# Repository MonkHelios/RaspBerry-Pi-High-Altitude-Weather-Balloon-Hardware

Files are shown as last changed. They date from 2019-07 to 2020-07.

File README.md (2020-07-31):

# Raspberry Pi Powered High Altitude Weather Balloon:

**The hardware of the weather balloon or the payload section is structured as a six layered stack of Raspberry Pi hats.**

---



- [x] The first layer is a _**Raspberry Pi**_ which manages operation of all other stacks and undertakes necessary processing tasks.
- [x] To power the entire stack we have a high current DC-DC converter as a _**power delivery unit**_ which accepts 1S LiPo or LiIon batteries as input and outputs a steady 5V and allows a maximum current draw of 7A.
- [x] For telemetry and other communication purposes we are using a _**CC1125 based RF board**_.
- [x] The next stack comprises of a _**GSM board**_ for non LOS communication at lower altitudes and a _**GPS board**_ for tracking the balloon and for easy retrieval. Since both of these are using the same serial channel of the Raspberry Pi, multiplexing and demultiplexing were necessary. This was facilitated by a _**Mux Demux board**_ which had the ability to select one peripheral among the two.
- [ ] Finally on top of the GPS hat we have the _**sensor hat**_.

---

## 1. Power Delivery Board (PiPo):

To run the essential hardware stacks a power delivery system more capable than a Raspberry Pi's internal power distribution was required. A design of a power distribution stack which could supply a high enough current with stability was adopted. The board was powered with a 3.7V LiIon or LiPo cell, its output was a constant 5V with a maximum allowed current of 7A. Our required peak current was 5A so, a 2A headroom was kept. The design was built around the _**LTC1871-1**_ - a wide input range, current mode, boost, flyback or SEPIC controller that drives an N-channel power MOSFET and requires very few external components.

### 1.1. Schematic:

<p align="center">
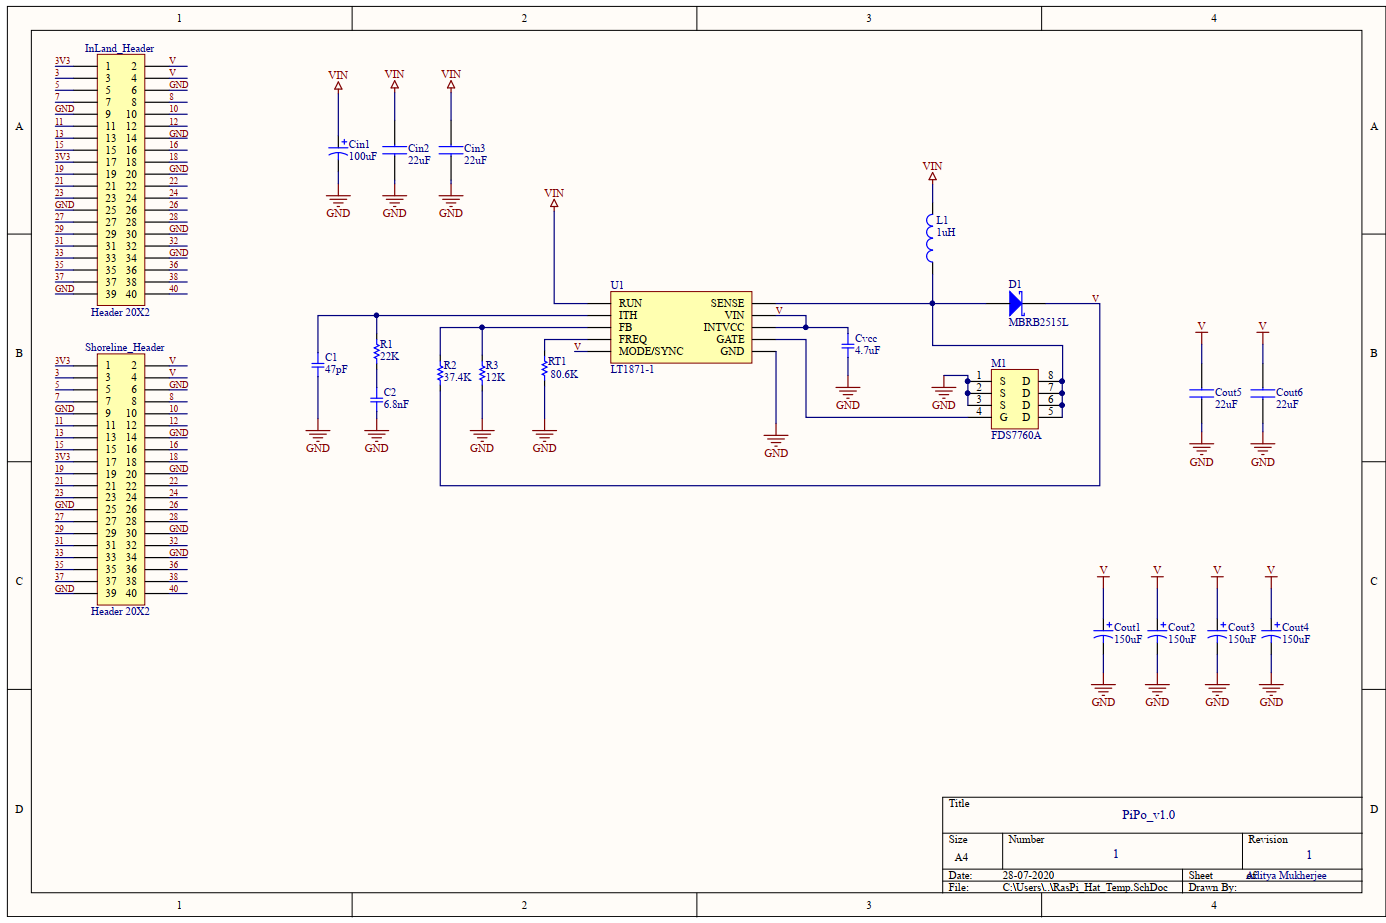
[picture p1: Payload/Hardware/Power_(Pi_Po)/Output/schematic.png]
  
</p>

[Link to PDF](https://github.com/MonkHelios/RaspBerry-Pi-High-Altitude-Weather-Balloon-Hardware/blob/master/Payload/Hardware/Power_(Pi_Po)/Output/schematic.pdf)

### 1.2. Composite:

<p align="center">
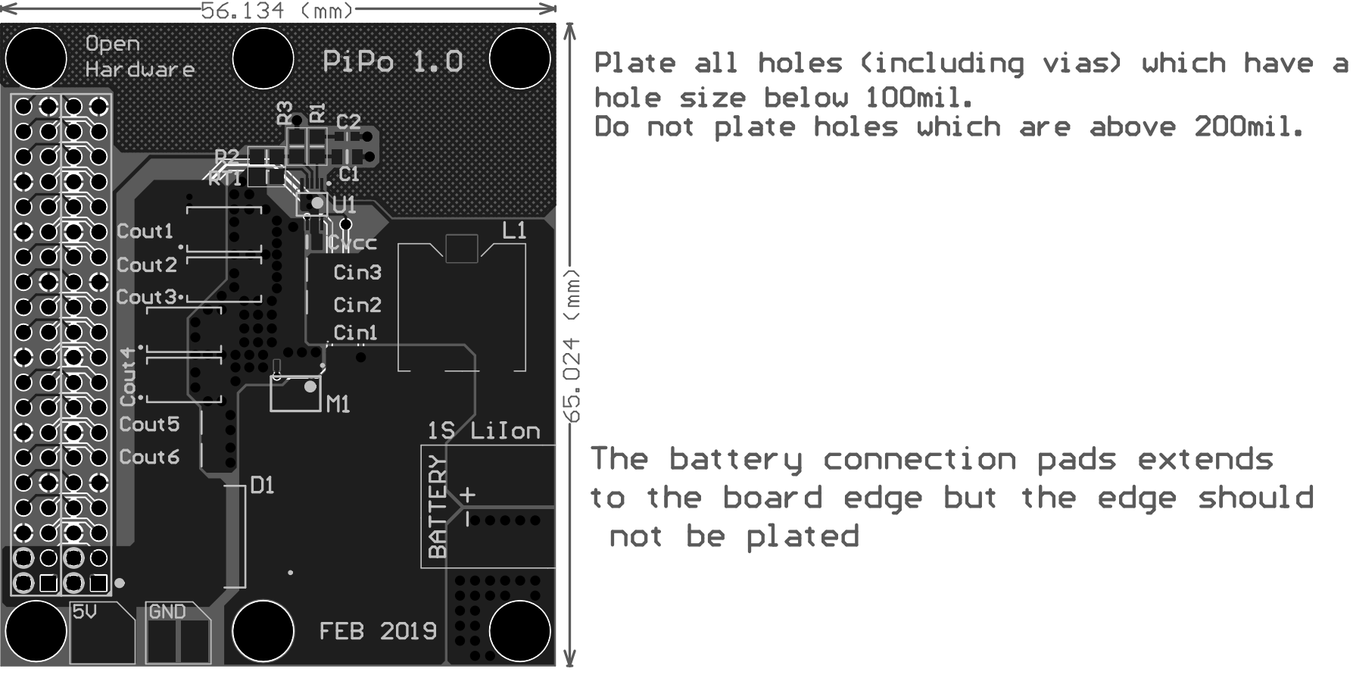
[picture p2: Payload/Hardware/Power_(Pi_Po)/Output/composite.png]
  
</p>

### 1.3. Assembly:

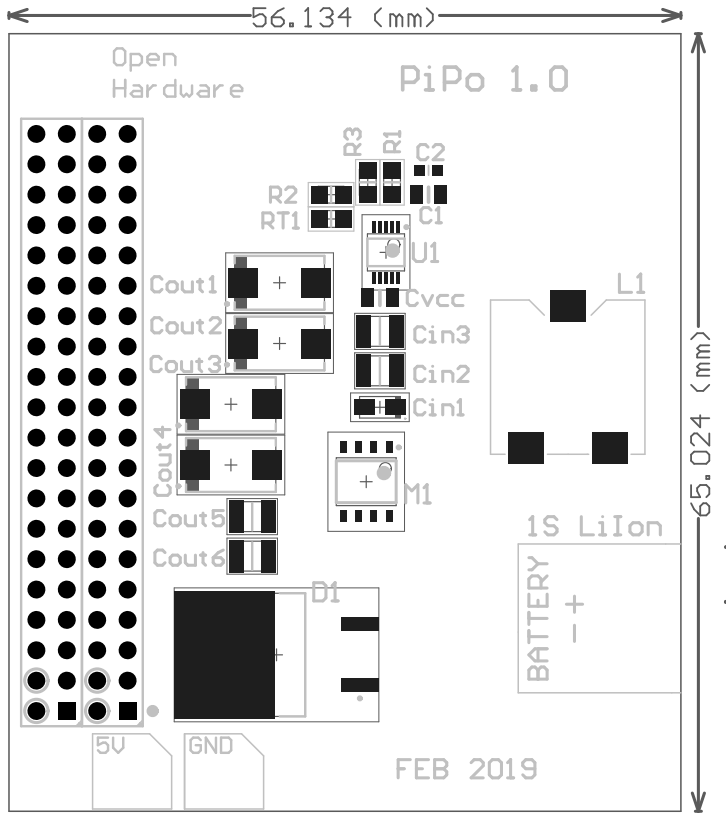
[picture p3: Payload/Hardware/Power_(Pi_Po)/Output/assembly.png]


**Comments on Revision 1.0 -** Assistance regarding _PCB layout, component placing & the schematic design_ was taken from the corresponding datasheets. Output voltage was as expected, as well as the ability to supply high currents. However, on probing the output with and oscilloscope it was found that the output waveform was quite noisy and had significant switching noise at the frequency of the used DC-DC converter. 

<br>

It was concluded that PCB layout and component placement were the culprits for induction of switching noise _(To be addressed in rev 2.0)_. Hence, I would not recommend following the component placement and PCB layout guides present in _**LTC1871-1's**_ datasheet. Instead, Understand the guidelines given and apply common mutual induction principles while designing the output section. 

<br>

<br>

---

## 2. Transceiver Board (LinkBerry):

For telemetry, real time location update and live image/video feed a point to point long distance RF link was designed and fabricated which is based on _Texas Instrument's_ _**CC1125**_ - a single chip, fully integrated narrow band RF transceiver. Coupled with a front end module (FEM) - _Qorvo's **RFFM6403**_, the board has a maximum output power level of **30dBm**. The FEM has inbuilt selectable power amplifier (PA) for transmission and a low noise amplifier (LNA) for reception. This communication stack acts as a bridge between the Pi's SPI bus and the unguided RF encoded & modulated data. In other words this encodes, modulates & transmits data received over the SPI bus (from the Pi). Also it decodes data received over its RF link and sends it through the SPI bus.
This is a 4 layer board since this includes mixed signal components, hence, strict PCB layout requirements. Also a thinner dielectric (prepreg) between the 50 Ohm RF traces and the GND plane allows for narrower RF microstrip lines for a given impedance. So, the layer stackup is important to keep in mind while designing.

### 2.1. Schematic:

[Link to PDF](https://github.com/MonkHelios/RaspBerry-Pi-High-Altitude-Weather-Balloon-Hardware/blob/master/Payload/Hardware/Transceiver_(LinkBerry)/Output/Radio.pdf)
_because component labels are too small for an image here._

`CC1125's datasheet followed for 50 Ohm matching`

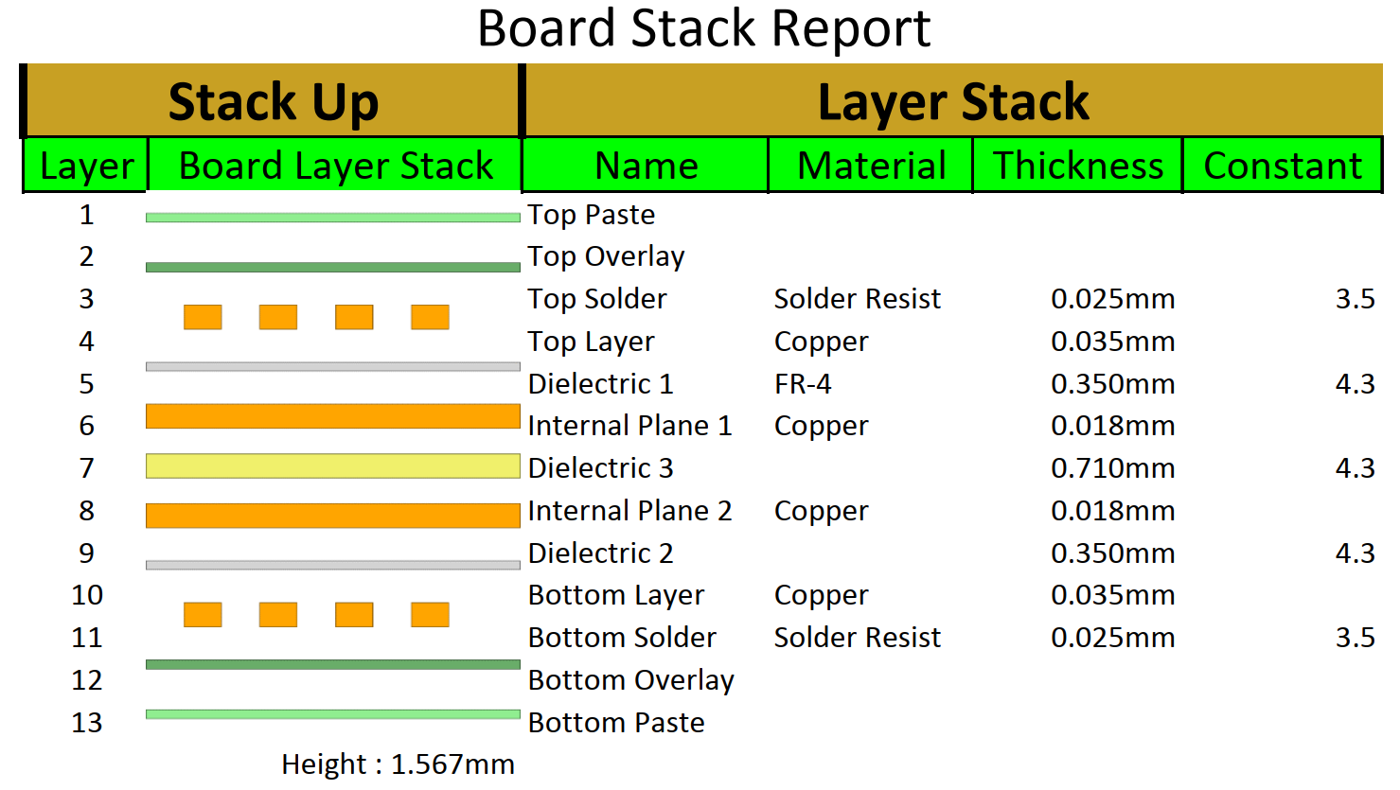
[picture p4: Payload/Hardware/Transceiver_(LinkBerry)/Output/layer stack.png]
### 2.2. Layer Stackup: 

- Top layer - separated digital and analog signals, most important signals are routed on this layer.
- Internal plane 1 - GND plane.
- Internal plane 2 - Power plane includes 3.3V, 3.6V & 5V polygons.
- Bottom layer - less important digital signals, traces which did not fit on the top layer, bridges and a GND polygon.

<br>

### 2.3. PCB layers:

<br>

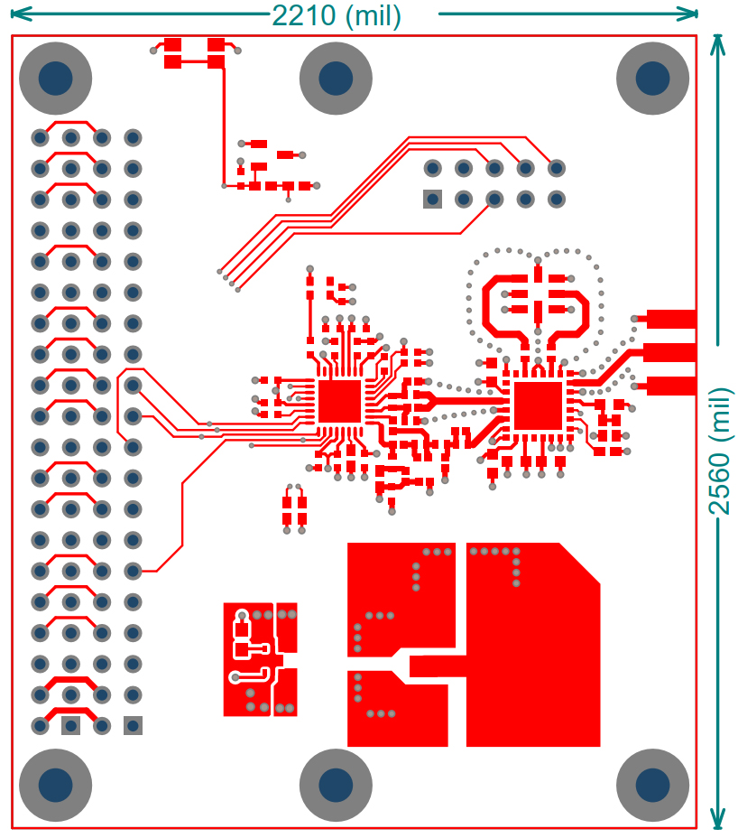
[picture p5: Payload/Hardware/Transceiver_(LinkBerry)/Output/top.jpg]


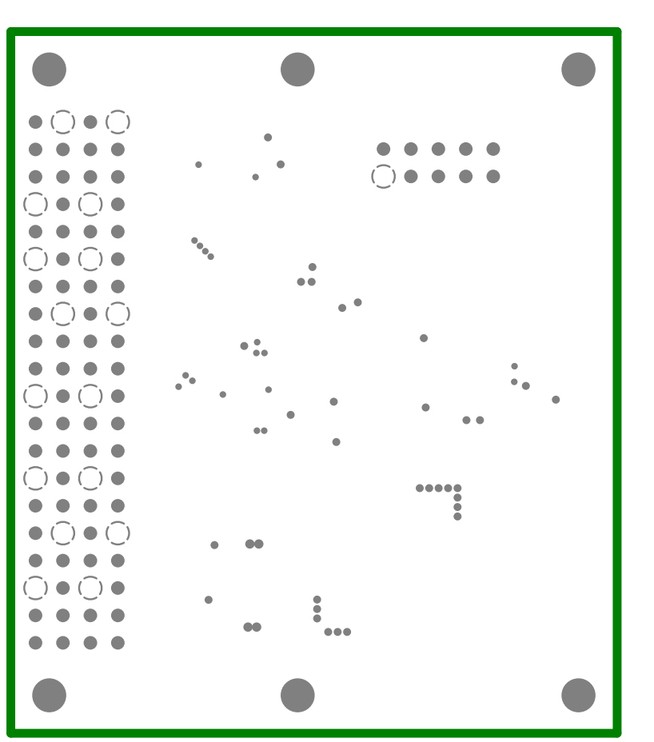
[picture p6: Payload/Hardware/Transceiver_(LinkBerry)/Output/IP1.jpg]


<p align="center">
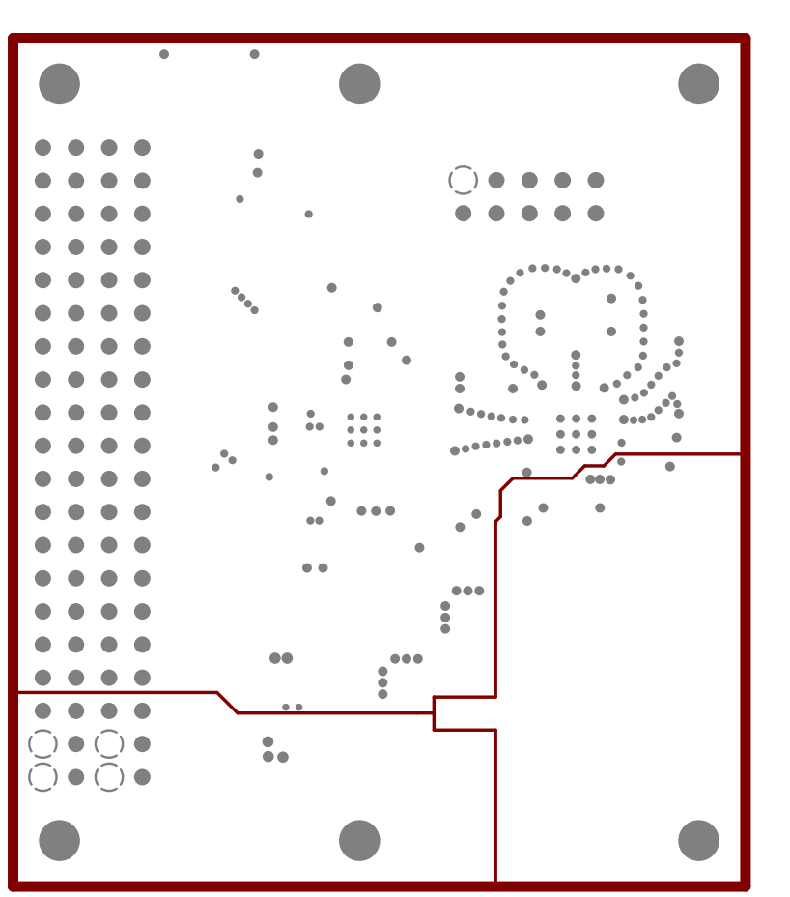
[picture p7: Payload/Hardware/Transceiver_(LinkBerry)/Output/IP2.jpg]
  
</p>

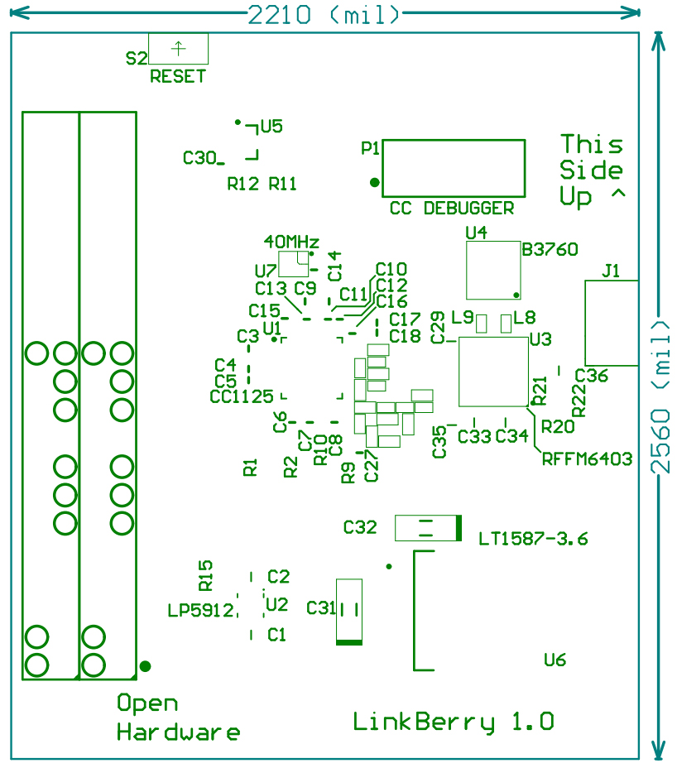
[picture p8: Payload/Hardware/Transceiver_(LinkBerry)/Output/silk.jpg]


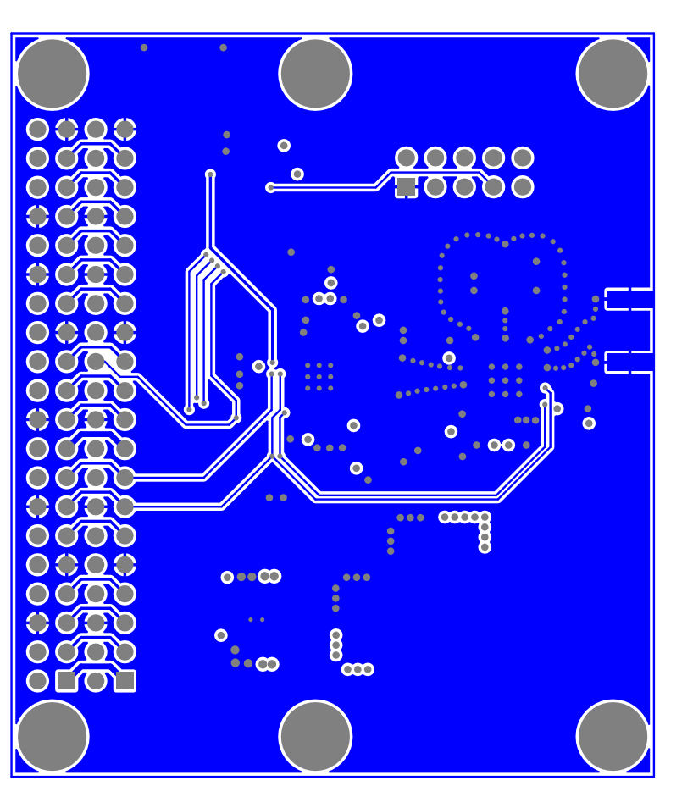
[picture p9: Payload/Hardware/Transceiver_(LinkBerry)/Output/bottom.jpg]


<p align="center">
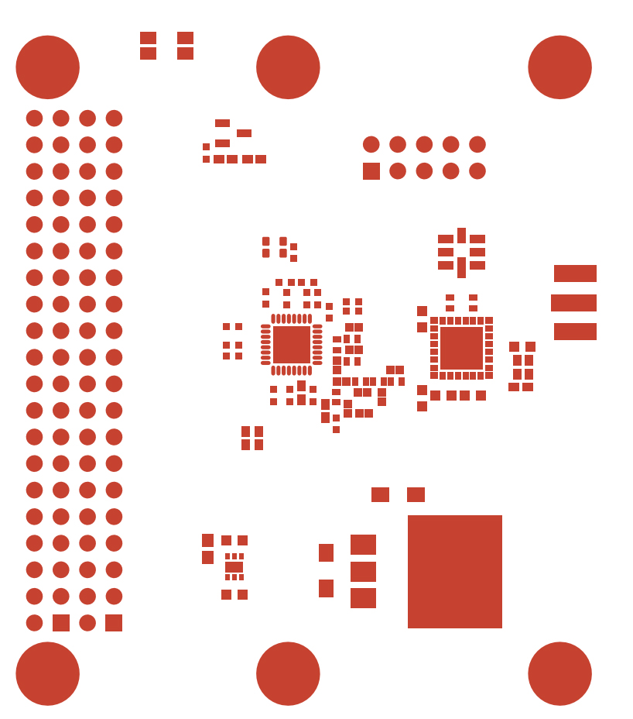
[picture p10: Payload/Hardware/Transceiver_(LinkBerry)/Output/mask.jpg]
  
</p>

<br>

<br>

### 2.4. Images:

<br>





<p align="center">
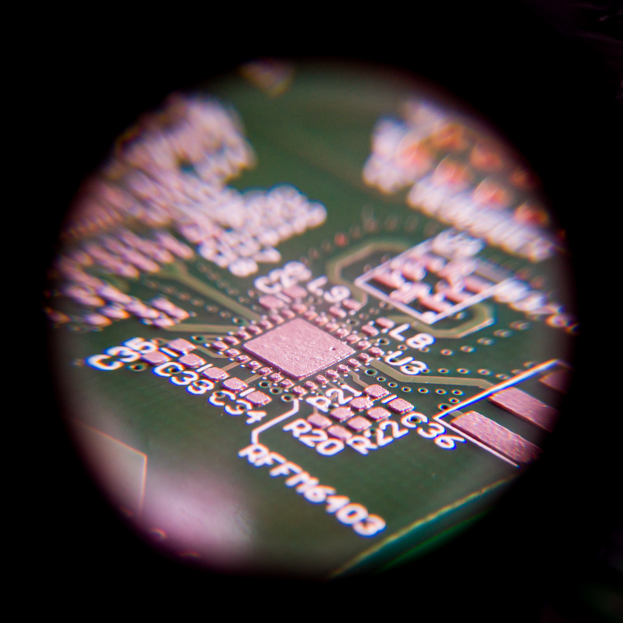
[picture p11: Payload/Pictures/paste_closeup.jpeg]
  
</p>
<br>

<br>

<br>

---

## 3. Multiplexer Board (PiMux):

This is a rather minimal 2:1 MUX board built around _**ISL54220**_ - a single supply dual 2:1 multiplexer that can operate from a single 2.7V to 5.5V supply. This multiplexes the two serial peripherals - GSM & GPS boards and enables them to be used one at a time on the single serial bus available on the Raspberry Pi. Data rates aren't a bottle neck as this IC was designed for USB purposes (480 Mbps).

### 3.1. Functional Diagram:

<p align="center">
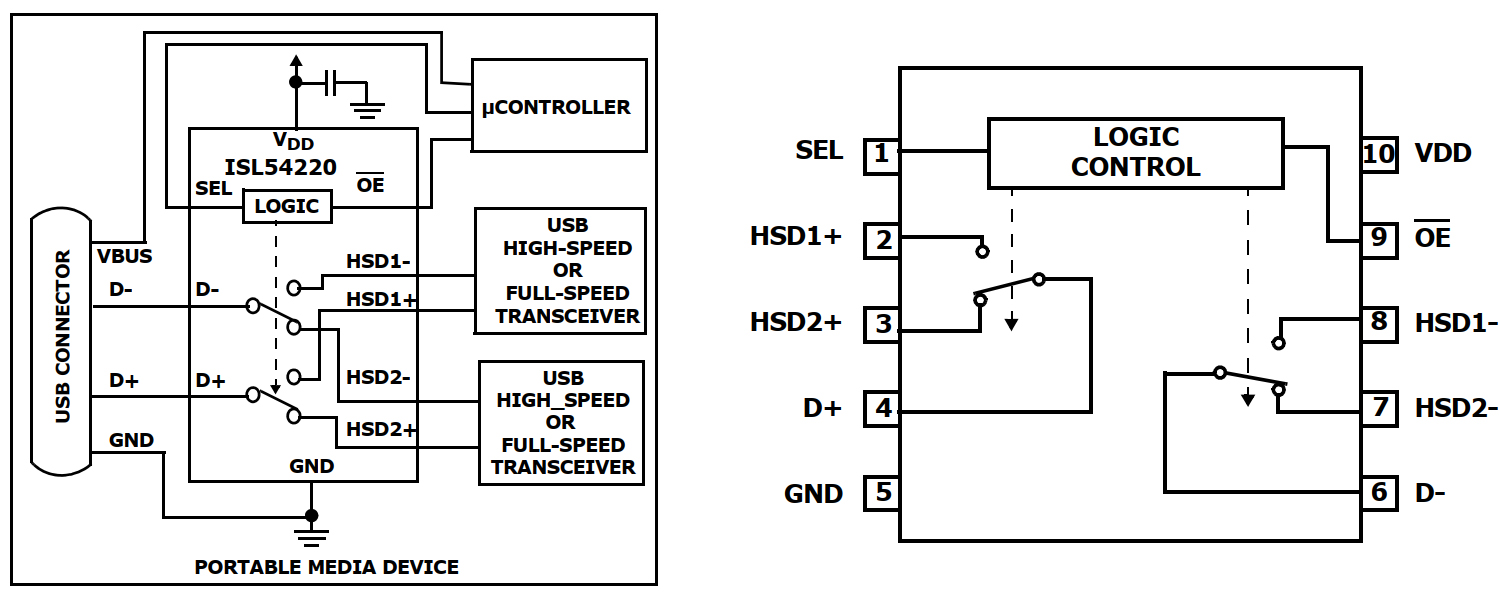
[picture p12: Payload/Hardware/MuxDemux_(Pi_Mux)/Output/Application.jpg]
  
</p>

<br>

### 3.2. Truth Table: 

<p align="center">
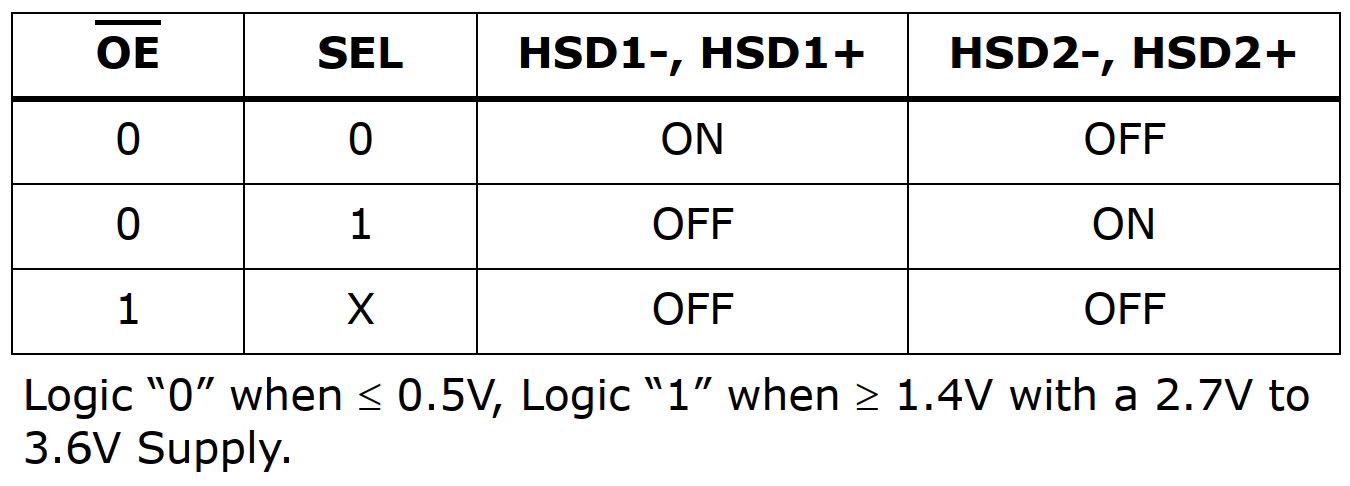
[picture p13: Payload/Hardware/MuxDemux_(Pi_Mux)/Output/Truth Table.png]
  
</p>

<br>

### 3.3. Schematic:

<p align="center">
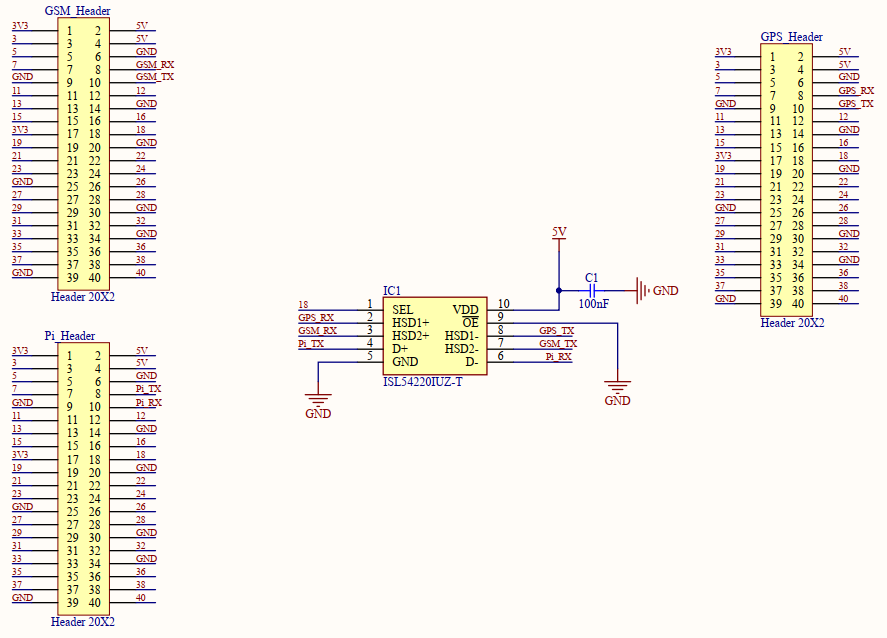
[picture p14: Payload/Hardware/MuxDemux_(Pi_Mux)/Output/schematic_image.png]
  
</p>

[Link to PDF](https://github.com/MonkHelios/RaspBerry-Pi-High-Altitude-Weather-Balloon-Hardware/blob/master/Payload/Hardware/MuxDemux_(Pi_Mux)/Output/schematic.pdf)

---

## 4. GSM board:

We used an available Raspberry Pi GSM hat made _**SmartElex**_. The primary purpose of GSM in this project would be to keep the communication link intact even if LOS communication is not possible. For example - maintaining comm link very near to ground where LOS might not be available. Also, for retrieval purposes the GPS and GSM board works hand in hand to provide the exact location where it landed. The GSM board is based on _**Quectel's M66**_ SMD module. So, relevant AT commands will be functional.

<p align="center">
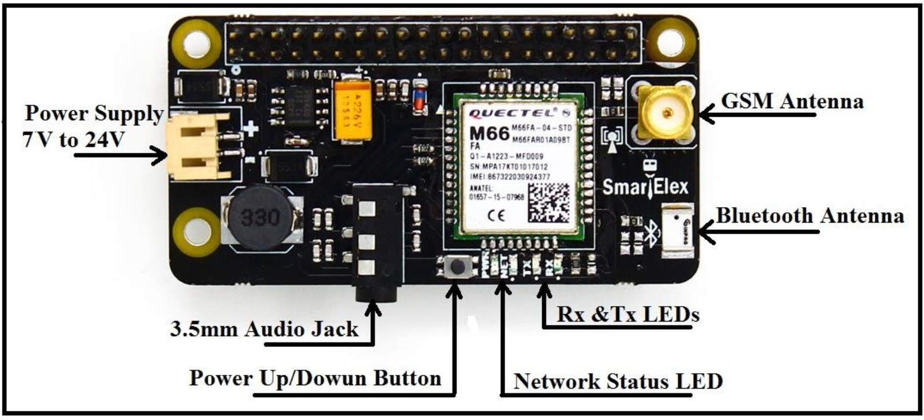
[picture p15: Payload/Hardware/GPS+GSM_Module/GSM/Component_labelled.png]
  
</p>

## 5. GPS board:  

Both GSM as well as the GPS boards used were purchased as a designed and fabricated board. This was because, in this particular application we did not require some special characteristic like we did in the case of the trancseiver board or the power distribution board. This GPS board is made by _**"Keyestudio"**_. Heart of the board is a _**"Ublox Neo-6M"**_ SMD GPS module.
Buying a ready made board instead of designing boards which already exist seemed practical and less costly.

<p align="center">
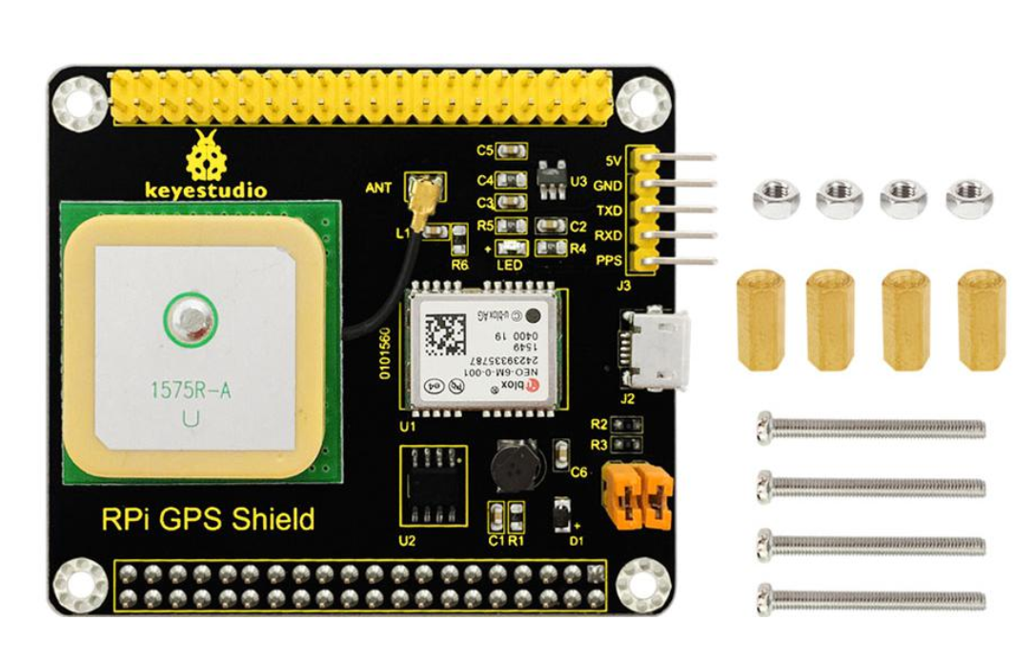
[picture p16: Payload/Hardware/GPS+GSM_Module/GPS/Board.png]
  
</p>

---

## 6. Sensor board (PiSense):

_Details about PiSense will be updated once design and fabrication are complete._

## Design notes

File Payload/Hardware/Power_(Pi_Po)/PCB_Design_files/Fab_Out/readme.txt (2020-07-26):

Gerber file identification:

The gerber files are named as per the layer information it provides.

drill files identification:

The drill files are named as per the drill type information it provides (palted or non plated).

*Plate all holes (including vias) which have a hole size below 100mil.
 Do not plate holes which are above 200mil.

layer stackup:

Your recommended stackup (1.6mm)

FAQ:

1. May we remove of non functional pads in inner layers? - There aren't any.
2. Adding copper thieving for better plating is allowed? - YES.
3. Is there any logo placement restrictions? - YES.
4. May we add “teardrop” at trace and pad intersections? - YES.
5. May we rim void if a land appears where a non-plated through-hole is placed? - NO.
6. May we give gang opening to the fine pitch SMT packages if spacing does not permit for solder mask dam? - NO.
7. If hole size tolerances are not called out, may we use +/- 0.075 mm? - YES.
8. If PCB thickness tolerances are not called out, may we use +/- 10%? - YES.
9. If PCB size tolerance is not called out, may we use +/- 0.25 mm? - YES.

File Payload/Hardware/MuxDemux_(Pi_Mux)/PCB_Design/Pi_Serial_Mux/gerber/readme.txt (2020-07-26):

drill files identification:

The drill files are named as per the drill type information it provides (palted or non plated).

*Plate all holes (including vias) which have a hole size below 100mil.
 Do not plate holes which are above 200mil.

layer stackup:

Your default 2 layer stackup.

FAQ:

1. May we remove of non functional pads in inner layers? - There aren't any.
2. Adding copper thieving for better plating is allowed? - YES.
3. Is there any logo placement restrictions? - YES. (However you can place your tracking ID on the bottom side of the board)
4. May we add “teardrop” at trace and pad intersections? - NO.
5. May we rim void if a land appears where a non-plated through-hole is placed? - NO.
6. May we give gang opening to the fine pitch SMT packages if spacing does not permit for solder mask dam? - YES.
7. If hole size tolerances are not called out, may we use +/- 0.075 mm? - YES.
8. If PCB thickness tolerances are not called out, may we use +/- 10%? - YES.
9. If PCB size tolerance is not called out, may we use +/- 0.25 mm? - YES.

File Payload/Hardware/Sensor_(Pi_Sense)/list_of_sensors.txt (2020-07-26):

temperature - stack, battery, ambient_in, ambient_out.
humidity - ambient_in, ambient_out.
gyro - on_board.
accel - on_board.
pressure(altitude) - on_board.

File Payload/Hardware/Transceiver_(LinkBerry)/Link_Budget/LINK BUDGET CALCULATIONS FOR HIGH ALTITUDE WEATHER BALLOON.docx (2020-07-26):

LINK BUDGET CALCULATIONS FOR HIGH ALTITUDE WEATHER BALLOON

LINK DISTANCE: 500Km (LOS)

Free space loss:

D = 500Km

F = 433MHz

LFS = 32.45 + 20log(500) + 20log(433) = (32.45 + 53.97 + 52.73) dB = 139.15 dB

On board antenna:

Half wave dipole:

Gdipole = 5 dBi

GCS antenna:

3 director 1 reflector Yagi Uda antenna driven by half wave folded dipole:

Gyagi = 12 dBi

FOR BALLOON TO GCS COMMUNICATION:

PA LNA on balloon as well as GCS.

PballoonTX = 27 dBm

LTX = 2 dB

LRX = 2 dB

Lmisc = 1 Db

GRX_LNA = 14 dB

LINK BUDGET:

PRX = PTX + GRX_LNA + GTX + GRX – LTX – LFS – Lmisc – LRX

PRX = 27 + 14 + 5 + 12 – 2 – 139.15 – 1 – 2 = - 86.15 dBm

RX sensitivity (50 kbps) = -109 dBm

Margin = 109 – 86.15 = 22.85 dBm

FOR GCS TO BALLOON COMMUNICATION:

PA LNA on balloon as well as GCS.

PGCS_TX = 30 dBm

LTX = 2 dB

LRX = 2 dB

Lmisc = 1 Db

GRX_LNA = 14 dB

LINK BUDGET:

PRX = PTX + GRX_LNA + GTX + GRX – LTX – LFS – Lmisc – LRX

PRX = 30 + 14 + 12 + 5 – 2 – 139.15 – 1 – 2 = - 83.15 dBm

RX sensitivity (50 kbps) = -109 dBm

Margin = 109 – 83.15 = 25.85 dBm

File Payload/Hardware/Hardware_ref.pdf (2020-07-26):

# RAS_PI pinouts:

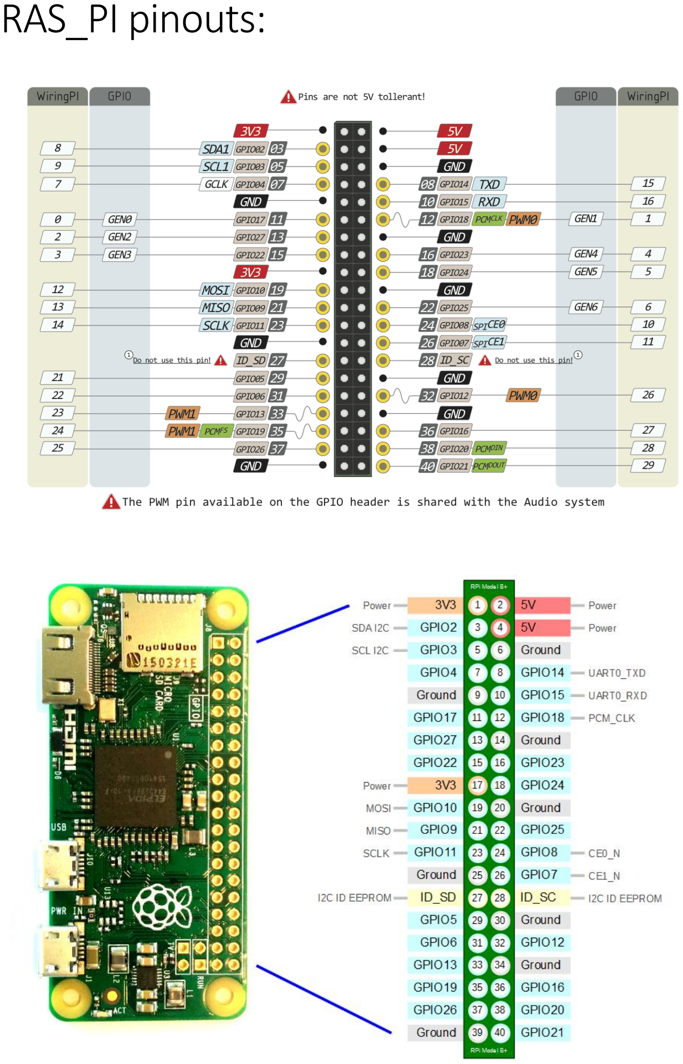
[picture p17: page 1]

# TELEMETRY BOARD:

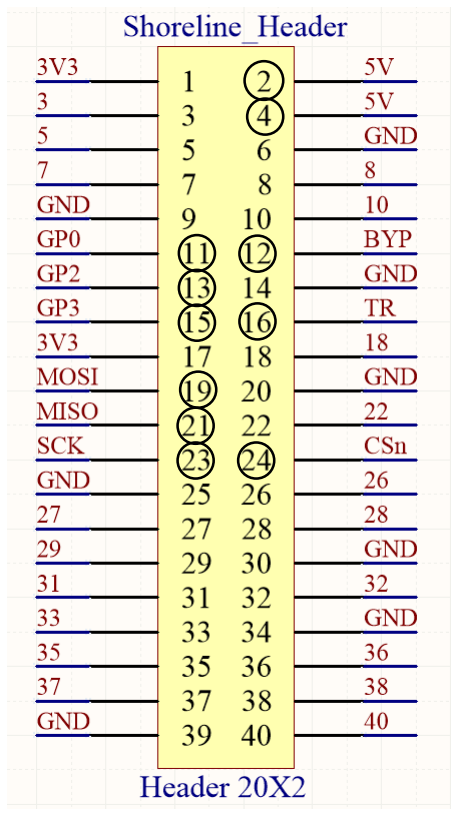
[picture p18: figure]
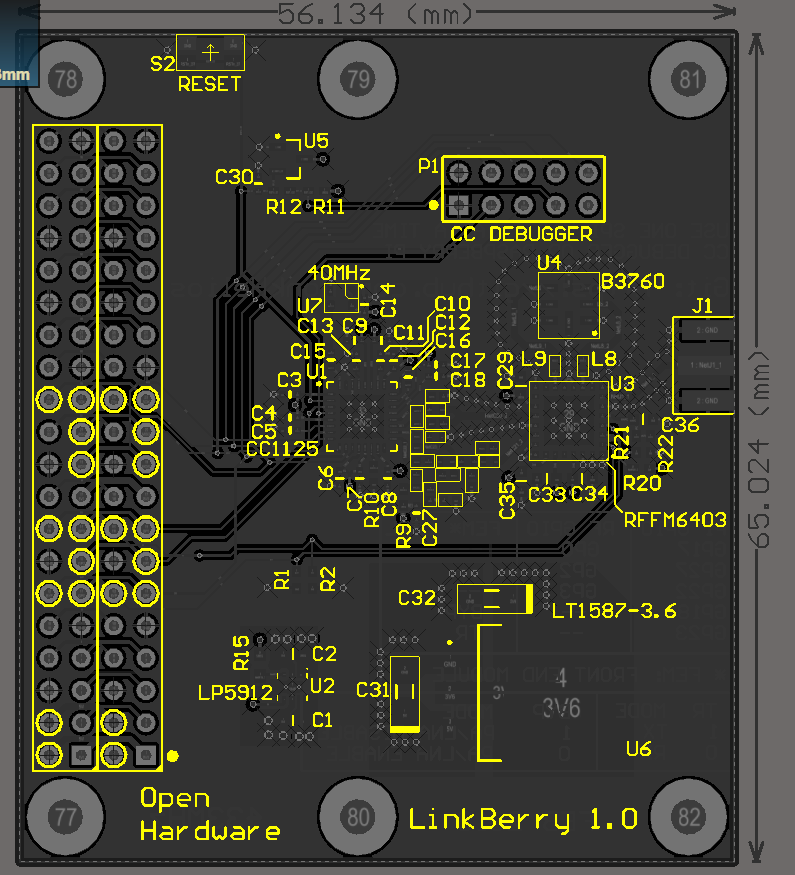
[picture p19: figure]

# Bidirectional SPI communication needs to be established between the Pi and the Telemetry board # Encircled pins are used by the telemetry board

# Rotate any one diagram by 180deg

# Pins 19, 21, 23, 24 are used for SPI communication between the Pi and the RF IC (CC1125, TI)

# Pins 11, 13, 15 are GPIO pins of the CC1125 (read CC1125 documentation for their usage)

# Pins 12, 16 are control pins of the front-end module (RFFM6403)

Header Pin No. | Pi GPIO | CC1125 GPIO | RFFM6403 CTRL
11 | GP17 | GP0 | -----
13 | GP27 | GP2 | -----
15 | GP22 | GP3 | -----
12 | GP18 | ----- | BYP
16 | GP23 | ----- | TR
TR | MODE
1 | TX
0 | RX
BYP | MODE
1 | PA/LNA Disable
0 | PA/LNA Enable

# GSM BOARD:

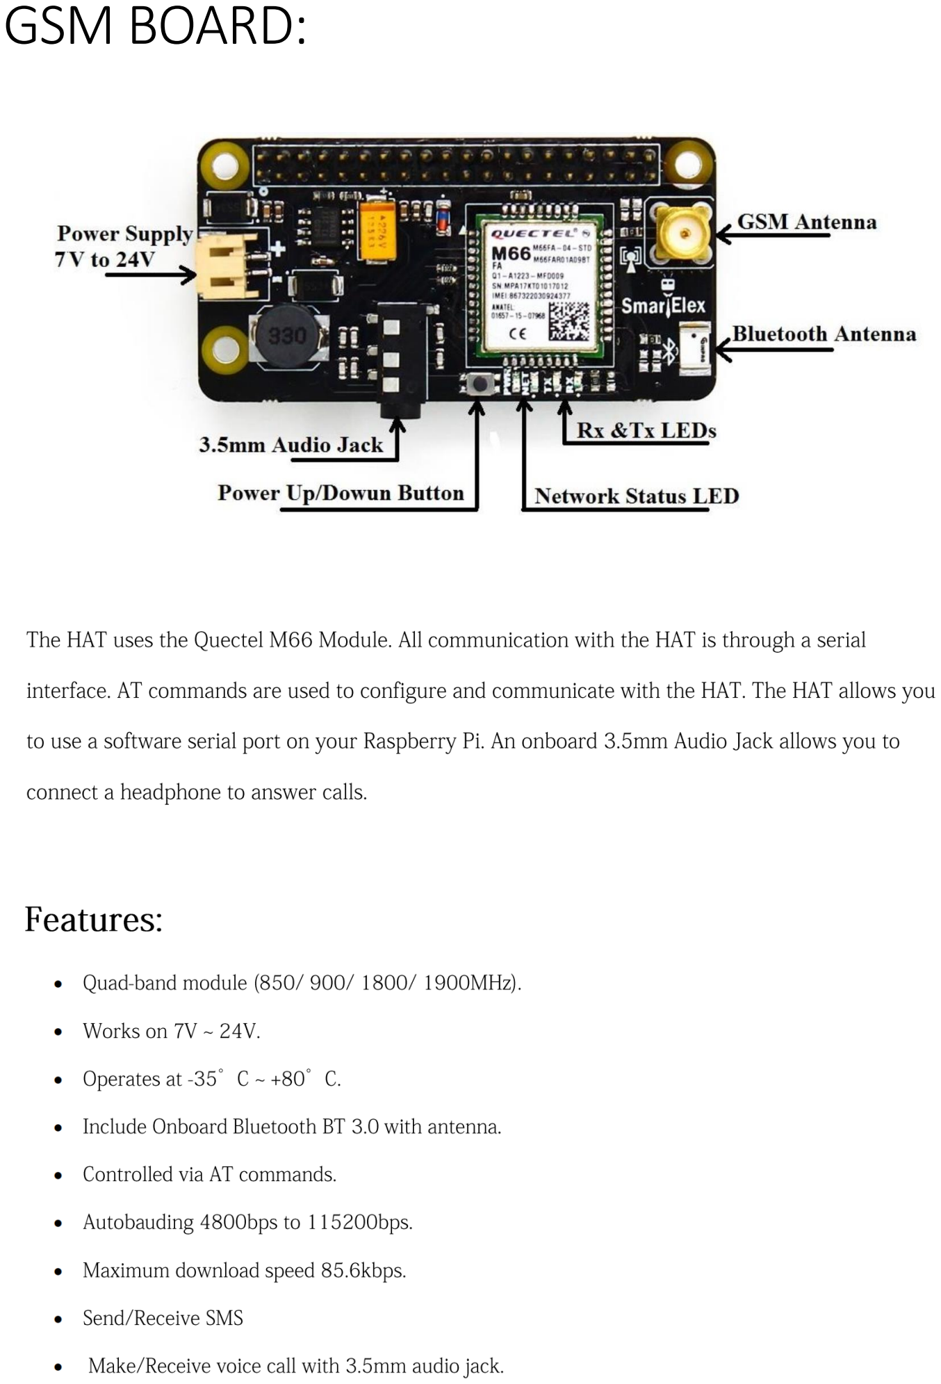
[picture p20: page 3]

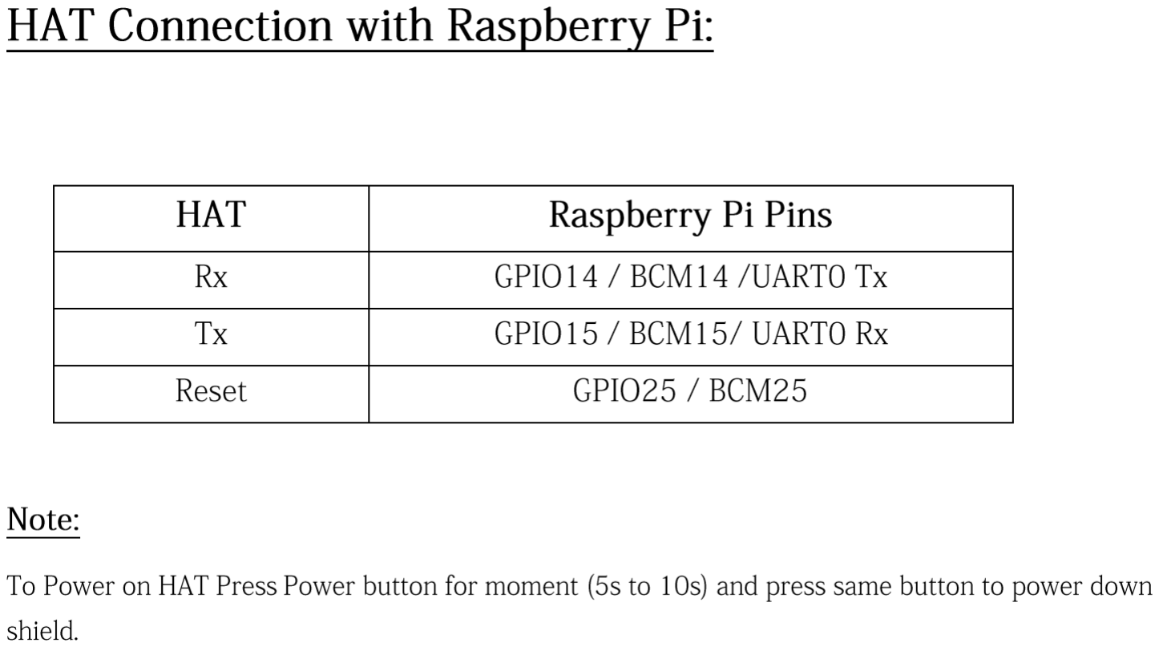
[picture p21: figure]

# GPS BOARD:

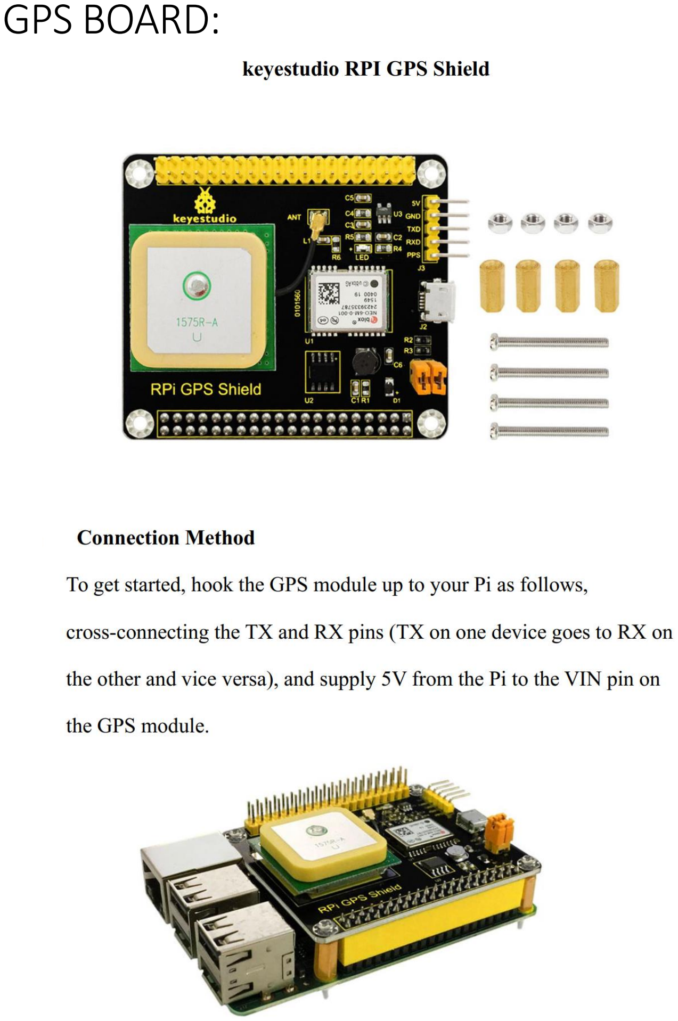
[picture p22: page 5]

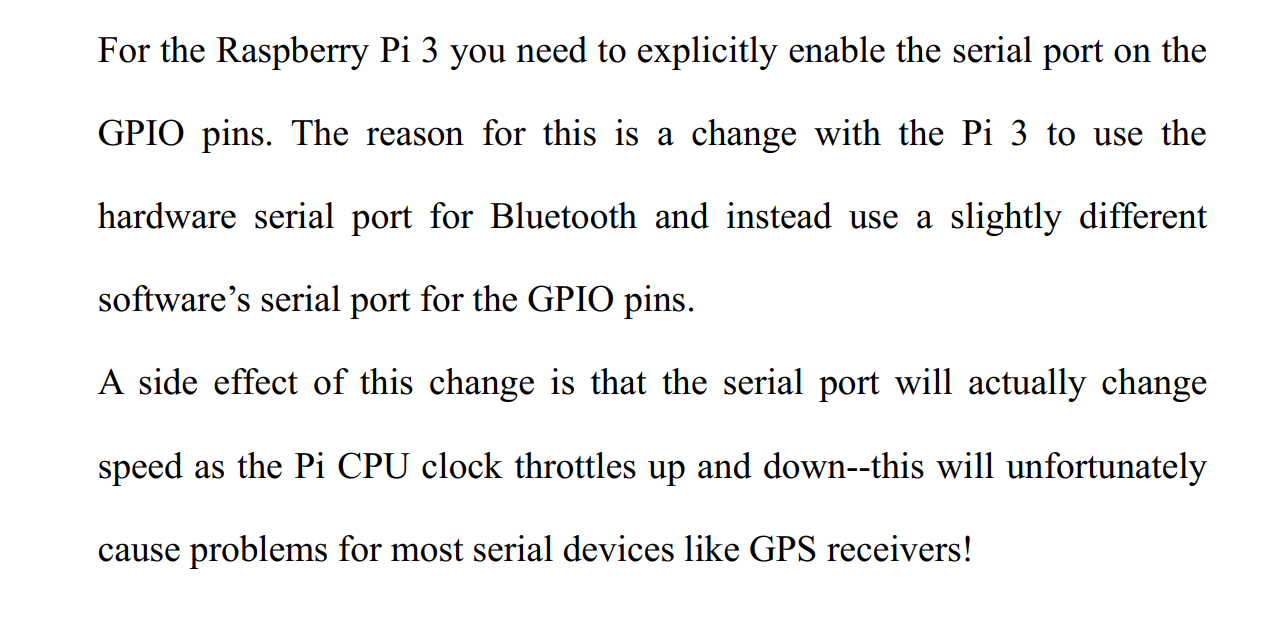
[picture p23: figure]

### # NOTE: GPS and GSM boards use the same two pins for serial

communication so, we need to mux and demux the RX and TX pins.

### # The GPIO pins for the mux and demux shall be updated once designed

### # Information about the sensor board shall also be updated once it is

designed, for now reserve the I2C bus for the sensors.

### # SPI communication between the telemetry board and Pi will also be

required at the ground station.

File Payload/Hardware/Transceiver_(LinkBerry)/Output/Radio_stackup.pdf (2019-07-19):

Layer | Board Layer Stack | Name | Material | Thickness | Constant

# Board Stack Report

Stack Up | Layer Stack

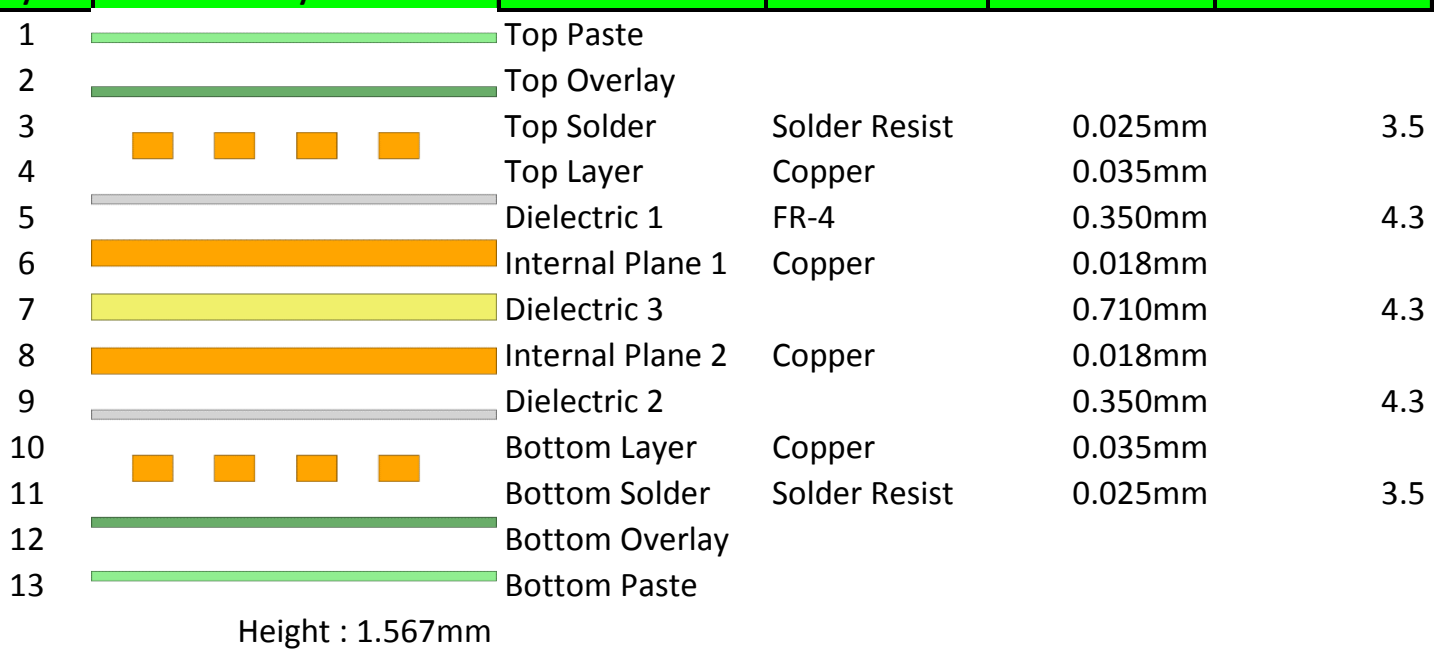
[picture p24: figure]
Top Paste; Top Overlay; Top Solder; Solder Resist; Top Layer; Copper; Dielectric 1; Internal Plane 1; Dielectric 3; Internal Plane 2; Dielectric 2; Bottom Layer; Bottom Solder; Bottom Overlay; Bottom Paste; Height : 1.567mm

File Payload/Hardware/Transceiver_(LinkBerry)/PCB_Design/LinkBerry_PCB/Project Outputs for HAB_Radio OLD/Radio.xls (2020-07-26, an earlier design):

Board Stack Report
Stack Up |  | Layer Stack
Layer | Board Layer Stack | Name | Material | Thickness | Constant
1 |  | Top Paste
2 |  | Top Overlay
3 |  | Top Solder | Solder Resist | 0.025mm | 3.5
4 |  | Top Layer | Copper | 0.035mm
5 |  | Dielectric 1 | FR-4 | 0.350mm | 4.3
6 |  | Internal Plane 1 | Copper | 0.018mm
7 |  | Dielectric 3 |  | 0.710mm | 4.3
8 |  | Internal Plane 2 | Copper | 0.018mm
9 |  | Dielectric 2 |  | 0.350mm | 4.3
10 |  | Bottom Layer | Copper | 0.035mm
11 |  | Bottom Solder | Solder Resist | 0.025mm | 3.5
12 |  | Bottom Overlay
13 |  | Bottom Paste
 | Height : 1.567mm

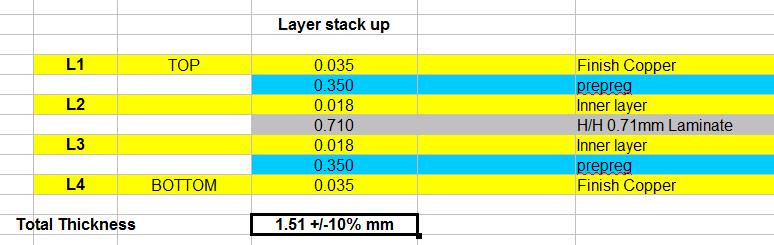
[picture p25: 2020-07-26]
Payload/Hardware/Transceiver_(LinkBerry)/PCB_Design/Fab_output/4Layer stackup.jpg

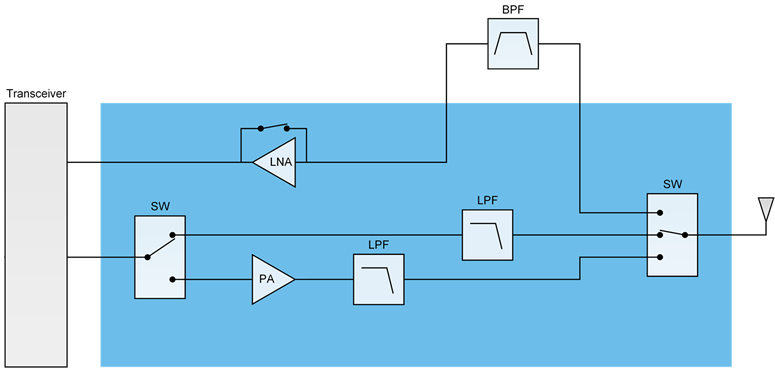
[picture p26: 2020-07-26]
Payload/Hardware/Transceiver_(LinkBerry)/Datasheets/amplifier/FEM_architecture.png

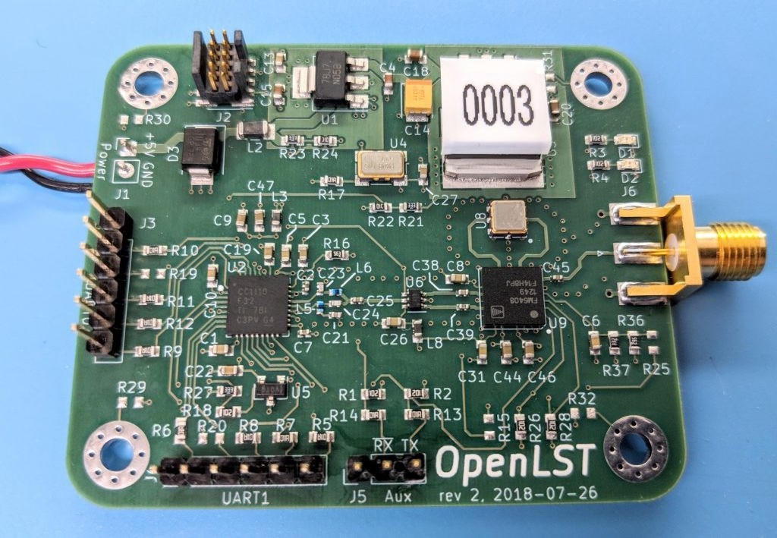
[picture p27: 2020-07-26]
Payload/Hardware/Transceiver_(LinkBerry)/Datasheets/amplifier/OpenLST.jpg

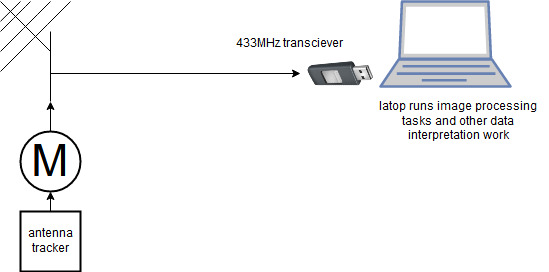
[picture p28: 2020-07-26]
GCS_Concept/gcs.jpg

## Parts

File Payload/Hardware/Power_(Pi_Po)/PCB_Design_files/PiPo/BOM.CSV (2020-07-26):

Comment | Pattern | Quantity | Components
100uF | TPSA226K006T0300 | 1 | Cin1 | 1206_TANTALUM
12K | Resistor_0805 | 1 | R3
150uF | EEF-CX0J151R | 4 | Cout1, Cout2, Cout3, Cout4
1uH | PCBComponent_1 | 1 | L1
22K | Resistor_0805 | 1 | R1
22uF | PCBComponent_1 | 4 | Cin2, Cin3, Cout5, Cout6
37.4K | Resistor_0805 | 1 | R2
4.7uF | SMD-0805C | 1 | Cvcc | CAP CER 10000PF 250V X5R 0805
47pF | SMD-0805C | 1 | C1 | CAP CER 10000PF 250V X7T 0805
6.8nF | SMD-0603C | 1 | C2 | CAP CER 0.1UF 16V X7R 0603
80.6K | Resistor_0805 | 1 | RT1
FDS7760A (IRF7463) | FDS7760A | 1 | M1 | IRF7463
Header 20X2 | HDR2X20 | 2 | InLand_Header, Shoreline_Header | Header, 20-Pin, Dual row
LT1871-1 | LTC1871-1 | 1 | U1
MBRB2515L | MBRB2515L | 1 | D1

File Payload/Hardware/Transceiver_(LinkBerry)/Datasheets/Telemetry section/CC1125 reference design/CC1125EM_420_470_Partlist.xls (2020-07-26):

CC1125 EM Rev 1.1.0 420-470 MHz version
Including LPF
Ref. | Part name | Pcs/unit | Description | Manufacturer | Part number | Supplier | Ordering code | Alt. Manufacturer | Alt. Part number | Alt. Supplier | Alt. Ordering code | Comments
C11 | C_47N_0402_X7R_K_25 | 1 | Capacitor, 47n, 0402, X7R, 10%, 25V | Murata | GRM155R71E473KA88D
C12 | C_100N_0402_X5R_K_10 | 0 | Do not mount
C41 | C_10N_0402_X7R_K_25 | 0 | Do not mount
C51 | C_47N_0402_X7R_K_25 | 1 | Capacitor, 47n, 0402, X7R, 10%, 25V | Murata | GRM155R71E473KA88D
C52 | C_2U2_0603_X5R_K_10 | 1 | Capacitor, 2u2, 0603, X5R, 10%, 10V | Murata | GRM188R61A225KE34D
C53 | C_0402 | 0 | Do not mount
C61 | C_220N_0402_X5R_K_10 | 1 | Capacitor, 220n, 0402, X5R, 10%, 10V | Murata | GRM155R61A224KE19D
C121 | C_47N_0402_X7R_K_25 | 1 | Capacitor, 47n, 0402, X7R, 10%, 25V | Murata | GRM155R71E473KA88D
C131 | C_47N_0402_X7R_K_25 | 1 | Capacitor, 47n, 0402, X7R, 10%, 25V | Murata | GRM155R71E473KA88D
C151 | C_47N_0402_X7R_K_25 | 1 | Capacitor, 47n, 0402, X7R, 10%, 25V | Murata | GRM155R71E473KA88D
C171 | C_10N_0402_X7R_K_25 | 1 | Capacitor, 10n, 0402, X7R, 10%, 25V | Murata | GRM155R71E103KA01D
C172 | C_100P_0402_NP0_J_50 | 1 | Capacitor, 100p, 0402, NP0, 5% 50V | Murata | GRM1555C1H101JZ01D
C173 | C_56P_0402_NP0_J_50 | 0 | Do not mount |  |  | #N/A | #N/A | #N/A | #N/A | #N/A | #N/A | #N/A
C174 | C_39P_0402_NP0_J_50 | 1 | Capacitor, 39p, 0402, NP0, 5%, 50V | Murata | GRM1555C1H390JZ01D
C175 | C_6P2_0402_NP0_C_50 | 1 | Capacitor, 6p2, 0402, NP0, +-0.25pF 50V | Murata | GRM1555C1H6R2CZ01D
C176 | C_2P2_0402_NP0_C_50 | 1 | Capacitor, 2p2, 0402, NP0, +-0.25pF, 50V | Murata | GRM1555C1H2R2CZ01
C177 | C_0402 | 0 | Do not mount
C181 | C_5P1_0402_NP0_C_50 | 1 | Capacitor, 5p1, 0402, NP0, +-0.25pF, 50V | Murata | GRM1555C1H5R1CZ01D
C191 | C_5P1_0402_NP0_C_50 | 1 | Capacitor, 5p1, 0402, NP0, +-0.25pF, 50V | Murata | GRM1555C1H5R1CZ01D
C201 | C_5P1_0402_NP0_C_50 | 1 | Capacitor, 5p1, 0402, NP0, +-0.25pF, 50V | Murata | GRM1555C1H5R1CZ01D
C211 | C_10N_0402_X7R_K_25 | 1 | Capacitor, 10n, 0402, X7R, 10%, 25V | Murata | GRM155R71E103KA01D
C221 | C_47N_0402_X7R_K_25 | 1 | Capacitor, 47n, 0402, X7R, 10%, 25V | Murata | GRM155R71E473KA88D
C231 | C_1N8_0402_U2J_J_10 | 1 | Capacitor, 1n8, 0402, U2J, 5%, 10V | Murata | GRM1557U1A182JA01D
C251 | C_47N_0402_X7R_K_25 | 1 | Capacitor, 47n, 0402, X7R, 10%, 25V | Murata | GRM155R71E473KA88D
C261 | C_47N_0402_X7R_K_25 | 1 | Capacitor, 47n, 0402, X7R, 10%, 25V | Murata | GRM155R71E473KA88D
C271 | C_47N_0402_X7R_K_25 | 1 | Capacitor, 47n, 0402, X7R, 10%, 25V | Murata | GRM155R71E473KA88D
C281 | C_47N_0402_X7R_K_25 | 1 | Capacitor, 47n, 0402, X7R, 10%, 25V | Murata | GRM155R71E473KA88D
C291 | C_47N_0402_X7R_K_25 | 1 | Capacitor, 47n, 0402, X7R, 10%, 25V | Murata | GRM155R71E473KA88D
C301 | R_0_0402 | 1 | Resistor, 0 ohm, 0402 | Koa | RK73Z1ETTP | ELFA | 60-470-05
C302 | C_0402 | 0 | Do not mount
C311 | C_15P_0402_NP0_J_50 | 0 | Do not mount
C321 | C_100N_0402_X5R_K_10 | 1 | Capacitor, 100n, 0402, X5R, 10%, 10V | Murata | GRM155R71A104KA01D
C322 | C_22P_0402_NP0_J_50 | 1 | Capacitor, 22p, 0402, NP0, 5%, 50V | Murata | GRM1555C1H220JZ01D
L1 | L_BEAD_102_0402 | 1 | EMI filter bead, 0402 1k ohms Tape GHz Band Gen Use | Murata | BLM15HG102SN1D | ACTE
L171 | L_56N_0402_J_LQW | 1 | Inductor, 56n, 0402, ±5%, wire-wound type | Murata | LQW15AN56NJ00 | ACTE
L172 | L_15N_0402_J_LQW | 1 | Inductor, 15n, 0402, ±5%, wire-wound type | Murata | LQW15AN15NJ00D
L173 | L_43N_0402_J_LQW | 1 | Inductor, 43n, 0402, ±5%, wire-wound type | Murata | LQW15AN43NJ00 | ACTE
L174 | L_22N_0402_J_LQW | 1 | Inductor, 22n, 0402, ±5%, wire-wound type | Murata | LQW15AN22NJ00D | ACTE
L191 | L_56N_0402_J_LQW | 1 | Inductor, 56n, 0402, ±5%, wire-wound type | Murata | LQW15AN56NJ00 | ACTE
L192 | L_27N_0402_J_LQW | 1 | Inductor, 27n, 0402, ±5%, wire-wound type | Murata | LQW15AN27NJ00D | ACTE
L193 | L_15N_0402_J_LQW | 1 | Inductor, 15n, 0402, ±5%, wire-wound type | Murata | LQW15AN15NJ00D
L201 | L_27N_0402_J_LQW | 1 | Inductor, 27n, 0402, ±5%, wire-wound type | Murata | LQW15AN27NJ00D | ACTE
P1 | SMD_SOCKET_2x10 | 1 | SMD pinrow socket, .050 spacing, 2x10 | Samtec | SFM-110-02-SM-D-A-K-TR | Abacus |  | Suhner | 85-SMA-50-0-44 | AFU, Arrow |  | Yes
P2 | SMD_SOCKET_2x10 | 1 | SMD pinrow socket, .050 spacing, 2x10 | Samtec | SFM-110-02-SM-D-A-K-TR | Abacus |  | Suhner | 85-SMA-50-0-44 | AFU, Arrow |  | Yes
P3 | SMA_SMD | 1 | SMA connector, straight SMD-mount | Hus-Tsan Group Taiwan | SMA-10V21-TGG | EC Partner A/S | SMA-10V21-TGG
R12 | R_0_0402 | 0 | Do not mount | Koa | RK73Z1ETTP | ELFA | 60-470-05
R141 | R_56K_0402_F | 1 | Resistor, 56k ohms, 0402, ±1% | Koa | RK73H1ETTP5602F | ELFA | 60-488-96
R171 | R_18_0402_J | 1 | Resistor, 18 ohms, 0402, 5% | Koa | RK73H1ETTP18R0F (±1%) | ELFA | 60-472-11 | Vishay | 63MT607103 | Farnell
R321 | R_0402 | 0 | Do not mount | Koa | RK73Z1ETTP | ELFA | 60-470-05
R322 | R_0_0402 | 1 | Resistor, 0 ohm, 0402 | Koa | RK73Z1ETTP | ELFA | 60-470-05
U1 | CC112X | 1 | TI tranciver | Texas Instruments
U2 | TPS79930 | 0 | Do not mount |  |  |  | #N/A | #N/A | #N/A | #N/A
X1 | X_32.000/10/20/60/10 | 0 | Do not mount | Epson Toyocom | FA-128, 32MHZ, 10PPM, 10PF, 2x1.6mm, -40/+85C, 60ohms | ACTE | Q22FA1280009200
X2 | TG_5021CG | 1 | TCXO 40.000000MHz (2.5x2.0x0.9mm) Supply voltage: 3.0V | Epson Toyocom | TG_5021CG | ACTE | X1G003581000300 | ALPS | SSSS222700 | #N/A
 |  | 43

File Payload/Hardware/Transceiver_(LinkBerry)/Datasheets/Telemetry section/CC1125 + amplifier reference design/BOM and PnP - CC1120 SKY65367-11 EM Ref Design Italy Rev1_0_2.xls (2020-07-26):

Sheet: BOM
CC1120_SKY65367_Reference_Italy_Rev1.0.2 |  |  |  | 25th January 2015
QTY | REFDES | VALUE | MANUFACTURER | MANUFACTURER_PN | PACKAGE | DESCRIPTION
1 | R4 | 0R | Panasonic | ERJ3GEY0R00 | 0603 | Thick Film Chip Resistor
1 | C49 | 1.2pF | MURATA | GRM1555C1H1R2CZ01 | 0402 | Multilayer Ceramic
1 | C47 | 1.8nF | MURATA | GRM155R71H182KA01 | 0402 | Multilayer Ceramic
1 | L14 | 2.2nH | MURATA | LQG15HN2N2S02D | 0402
1 | J5 | 2X2 | Samtec | TSW-102-07-G-D | 100mil | 100mil Header
1 | J1 | 3X1 | Samtec | TSW-103-07-G-S | 100mil | 100mil Header
1 | C23 | 4.7nF | MURATA | GRM155R71H472KA01 | 0402 | Multilayer Ceramic
1 | L10 | 4.7nH | MURATA | LQG15HN4N7S02D | 0402
1 | L12 | 7.5nH | MURATA | LQG15HS7N5J02D | 0402
1 | J4 | 7X2 | Samtec | TSW-107-07-G-D | 100mil | 100mil Header
1 | L15 | 10nH | MURATA | LQG18HN10NJ00D | 0603
1 | FB1 | 10R | Murata | BLM15BB100SN1 | 0402 | Chip Ferrite Bead
1 | L13 | 15nH | MURATA | LQG15HN15NJ02D | 0402
1 | L6 | 18nH | MURATA | LQG15HS18NJ02D | 0402
1 | C44 | 18pF | MURATA | GRM1555C1H180JZ01 | 0402 | Multilayer Ceramic
1 | L9 | 27nH | MURATA | LQG15HN27NJ02D | 0402 | High Frequency Multilayer
1 | L16 | 27nH | MURATA | LQG18HN27NJ00D | 0603
1 | C7 | 27pF | MURATA | GRM1555C1H270JZ01 | 0402 | Multilayer Ceramic
1 | Y1 | 32MHz | Epson-Toyocomm | FA-128 | SMD_2.0MMX1.6MM | Xtal 32MHz
1 | L11 | 33nH | MURATA | LQG18HN33NJ00D | 0603 | High Frequency Multilayer
1 | L5 | 39nH | MURATA | LQG15HS39NJ02D | 0402 | High Frequency Multilayer
1 | L17 | 47nH | MURATA | LQG18HN47NJ00D | 0603
1 | R6 | 56K | Panasonic | ERJ2GEJ563 | 0402 | Thick Film Chip Resistor
1 | L2 | 68nH | MURATA | LQG15HS68NJ02D | 0402 | High Frequency Multilayer
1 | C43 | 100nF | MURATA | GRM155R71C104KA88D | 0402 | Monolithic Ceramic
1 | L8 | 100nH | MURATA | LQG15HSR10J02 | 0402
1 | L18 | 100nH | MURATA | LQG18HNR10J00D | 0603 | High Frequency Multilayer
1 | C9 | 100pF | MURATA | GRM1555C1H101JZ01 | 0402 | Multilayer Ceramic
1 | L7 | 150nH | MURATA | LQG15HSR15J02D | 0402 | High Frequency Multilayer
1 | C29 | 220nF | MURATA | GRM155R60J224KE01 | 0402 | Multilayer Ceramic
1 | L1 | 220nH | MURATA | LQG15HSR22J02D | 0402
1 | FB3 | 600R | Murata | BLM15BD601SN1 | 0402 | Chip Ferrite Bead
1 | U2 | AA116-72LF | Skyworks Solutions Inc. | AA116-72LF | SOT23-5 | 4 MHz to 2 GHz 1-Bit Digital Attenuator
1 | FB2 | BLM15AG100SN1D | Murata | BLM15AG100SN1D | 0402 | Chip Ferrite Bead
1 | U3 | CC1120 | TI | CC1120 | QFN5X5-32 | High Performance RF Transceiver for Narrowband Systems
1 | U1 | SKY65367-11 | Skyworks Solutions Inc. | SKY65367-11 | MCM400X400-16 | 169-170 MHz Transmit/Receive Front-End Module
1 | J3 | SMA | Johnson Components | 142-0701-201 | through hole | SMA Straight PC Mount Jack Receptacle
2 | R2,R12 | 0R | Panasonic | ERJ2GEJ0R0 | 0402 | Thick Film Chip Resistor
1 | C17 | 1nF | MURATA | GRM1555C1H102JA01 | 0402 | Multilayer Ceramic
2 | C19,C24 | 1uF | MURATA | GRM155R60J105KE19 | 0402 | Multilayer Ceramic
2 | C3,C4 | 10nF | MURATA | GRM155R71E103KA01 | 0402 | Multilayer Ceramic
2 | J2,J6 | 10X2 | Samtec | SFM-110-02-S-D-A | 50mil | 50mil Female Header
2 | C16,C25 | 22pF | MURATA | GRM1555C1H220JZ01 | 0402 | Multilayer Ceramic
2 | R5,R7 | 47K | Panasonic | ERJ2GEJ473 | 0402 | Thick Film Chip Resistor
2 | L3,L4 | 82nH | MURATA | LQG15HS82NJ02D | 0402 | High Frequency Multilayer
2 | C12,C21 | 82pF | MURATA | GRM1555C1H820JZ01 | 0402 | Multilayer Ceramic
3 | C5,C8,C46 | 2.2uF | MURATA | GRM188R71A225KE15D | 0603 | Monolithic Ceramic
3 | C13,C14,C15 | 15pF | MURATA | GRM1555C1H150JZ01 | 0402 | Multilayer Ceramic
3 | R8,R9,R10 | 100K | Panasonic | ERJ2GEJ104 | 0402 | Thick Film Chip Resistor
4 | C1,C2,C18,C30 | 12pF | MURATA | GRM1555C1H120JZ01 | 0402 | Multilayer Ceramic
5 | C6,C11,C22,C45,C48 | 2.2nF | MURATA | GRM155R71H222KA01 | 0402 | Multilayer Ceramic
11 | C32,C33,C34,C35,C36, C37,C38,C39,C40,C41,C42 | 47nF | MURATA | GRM155R71E473KA88 | 0402 | Multilayer Ceramic
0 | C20,C28,C31 | DNI | - | - | 0402 | -
0 | R1,R11 | DNI |  |  | 0402 | Do Not Install
0 | C26 | DNI / 1nF | MURATA | GRM1555C1H102JA01 | 0402 | Multilayer Ceramic
0 | R3 | DNI / 0R | Panasonic | ERJ2GEJ0R0 | 0402 | Thick Film Chip Resistor
0 | C10 | DNI / 22pF | MURATA | GRM1555C1H220JZ01 | 0402 | Multilayer Ceramic
0 | Y2 | DNI / 40MHz | Epson-Toyocomm | TG-5021CG | SMD_2.5MMX2.0MM | TCXO 2V8
0 | C27 | DNI / 100nF | MURATA | GRM155R71C104KA88D | 0402 | Monolithic Ceramic
0 | ANT1 | DNI / ANT-COIL-169MHZ | Pulse | W3100 | - | Helical Antenna

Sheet: PnP
RefDes | Layer | X | Y
ANT1 | Top | 227.185 | 170.5
C1 | Top | 221.2 | 135.7
C2 | Top | 219.4 | 135.7
C3 | Top | 226.73 | 131.995
C4 | Top | 218.3 | 135
C5 | Top | 206.397 | 136.77
C6 | Top | 225.127 | 144.05
C7 | Top | 219.887 | 163.47
C8 | Top | 222.98 | 122.625
C9 | Top | 226.73 | 132.995
C10 | Top | 214.9 | 123.9
C11 | Top | 225.127 | 150.96
C12 | Top | 223.6 | 134
C13 | Top | 213.4 | 124.3
C14 | Top | 211.6 | 125.9
C15 | Top | 224.6 | 139.925
C16 | Top | 222.394 | 158.621
C17 | Top | 213.645 | 155.41
C18 | Top | 225.1 | 135.4
C19 | Top | 212.665 | 155.41
C20 | Top | 210.7 | 125.9
C21 | Top | 216.09 | 163.47
C22 | Top | 223.655 | 146.73
C23 | Top | 213.685 | 159.62
C24 | Top | 212.665 | 159.62
C25 | Top | 216.937 | 151.925
C26 | Top | 223.085 | 139.42
C27 | Top | 213.5 | 123.3
C28 | Top | 214.665 | 155.4
C29 | Top | 221.3 | 125.5
C30 | Top | 224.6 | 136.895
C31 | Top | 216.937 | 154.925
C32 | Top | 216.9 | 125.4
C33 | Top | 219.6 | 125.2
C34 | Top | 224.2 | 128.6
C35 | Top | 223.9 | 129.9
C36 | Top | 223.9 | 131.7
C37 | Top | 217.4 | 135.2
C38 | Top | 214.1 | 129.1
C39 | Top | 214.7 | 130.4
C40 | Top | 214.7 | 131.4
C41 | Top | 215 | 132.3
C42 | Top | 210.8 | 128.3
C43 | Top | 206.395 | 132.3
C44 | Top | 226.194 | 158.621
C45 | Top | 219.887 | 161.47
C46 | Top | 223 | 119.6
C47 | Top | 216.4 | 133.7
C48 | Top | 220.765 | 139.7
C49 | Top | 225.1 | 141.425
FB1 | Top | 224.8 | 121.85
FB2 | Top | 224.8 | 120.4
FB3 | Top | 212.665 | 157.56
J1 | Top | 203.415 | 131.795
J2 | Bottom | 204.56 | 126.72
J3 | Top | 232.844 | 159.121
J4 | Top | 203.415 | 164.795
J5 | Top | 232.057 | 148.76
J6 | Bottom | 235.04 | 126.72
L1 | Top | 223.6 | 133
L2 | Top | 224.1 | 141.425
L3 | Top | 222.1 | 135.7
L4 | Top | 220.3 | 135.7
L5 | Top | 220.765 | 137.705
L6 | Top | 224.1 | 135.4
L7 | Top | 220.7 | 134.1
L8 | Top | 224.1 | 138.42
L9 | Top | 217.437 | 153.425
L10 | Top | 226.194 | 156.621
L11 | Top | 226.44 | 162.28
L12 | Top | 216.09 | 161.22
L13 | Top | 215.987 | 157.52
L14 | Top | 216.09 | 165.37
L15 | Top | 215.587 | 159.12
L16 | Top | 217.99 | 162.97
L17 | Top | 224.294 | 159.121
L18 | Top | 227.185 | 164.37
PCB1 | Top | 216.135 | 136.63
R1 | Top | 210.8 | 127.4
R2 | Top | 215.8 | 125.4
R3 | Top | 211.7 | 122.6
R4 | Top | 227.185 | 167.17
R5 | Top | 208.415 | 132.35
R6 | Top | 223.9 | 130.8
R7 | Top | 208.415 | 131.26
R8 | Top | 208.45 | 164.79
R9 | Top | 208.45 | 154.64
R10 | Top | 208.45 | 152.09
R11 | Top | 227.194 | 159.621
R12 | Top | 227.694 | 159.121
U1 | Top | 219.087 | 158.32
U2 | Top | 226.427 | 147.23
U3 | Top | 219.3 | 129.6
Y1 | Top | 213.3 | 126.2
Y2 | Top | 213.825 | 121.505

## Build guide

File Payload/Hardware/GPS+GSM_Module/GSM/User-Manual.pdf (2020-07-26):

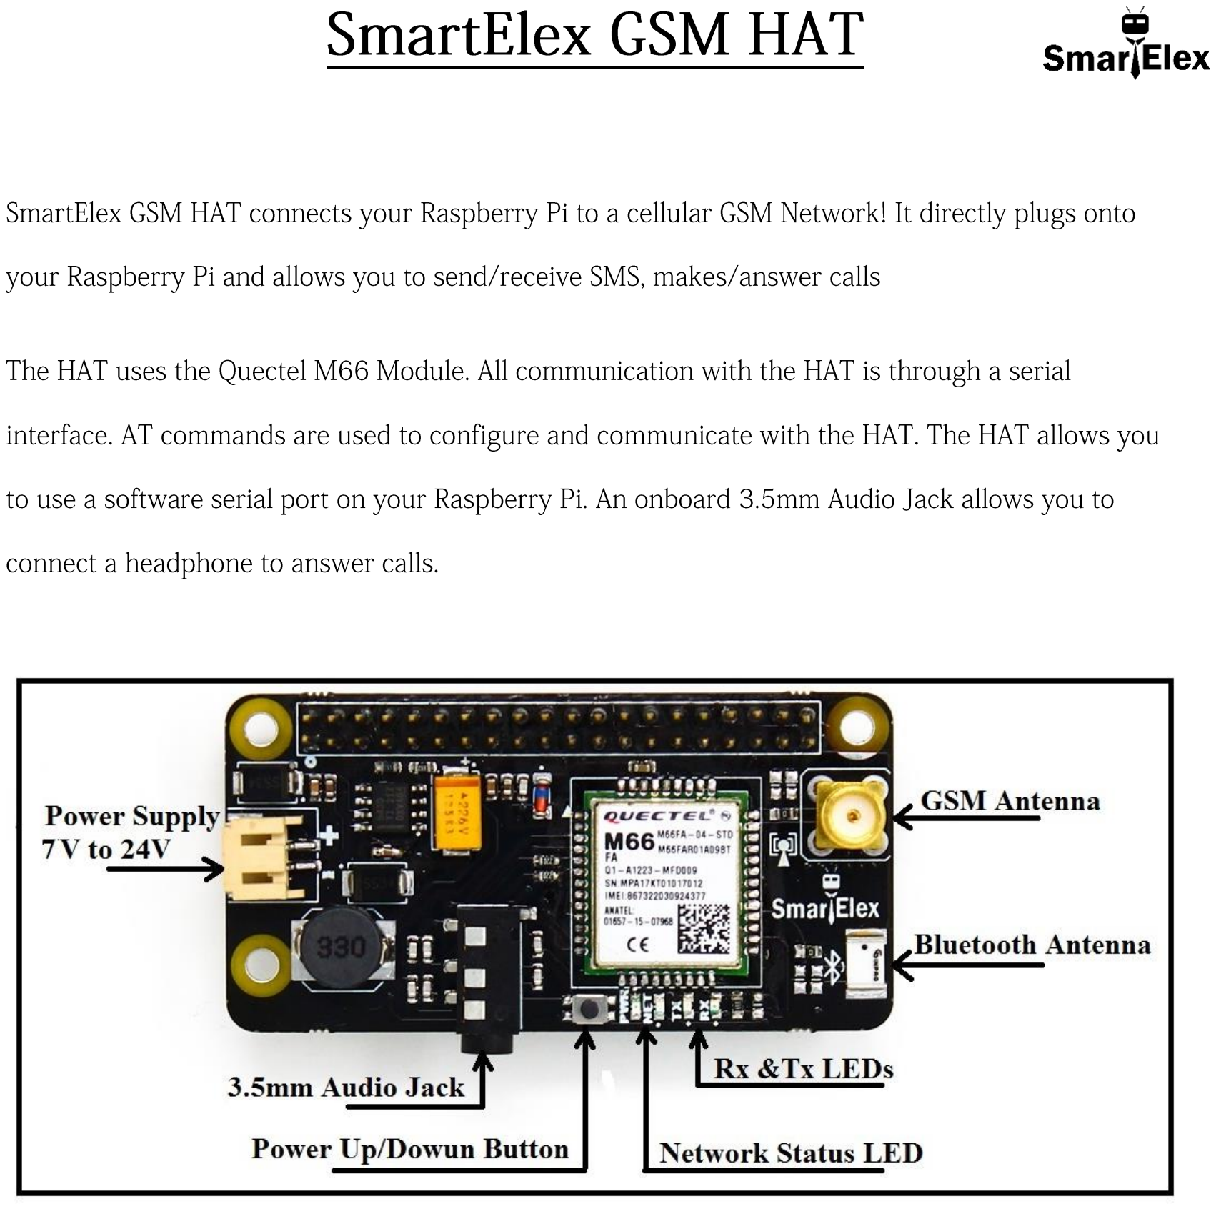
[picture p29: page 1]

•••••••••

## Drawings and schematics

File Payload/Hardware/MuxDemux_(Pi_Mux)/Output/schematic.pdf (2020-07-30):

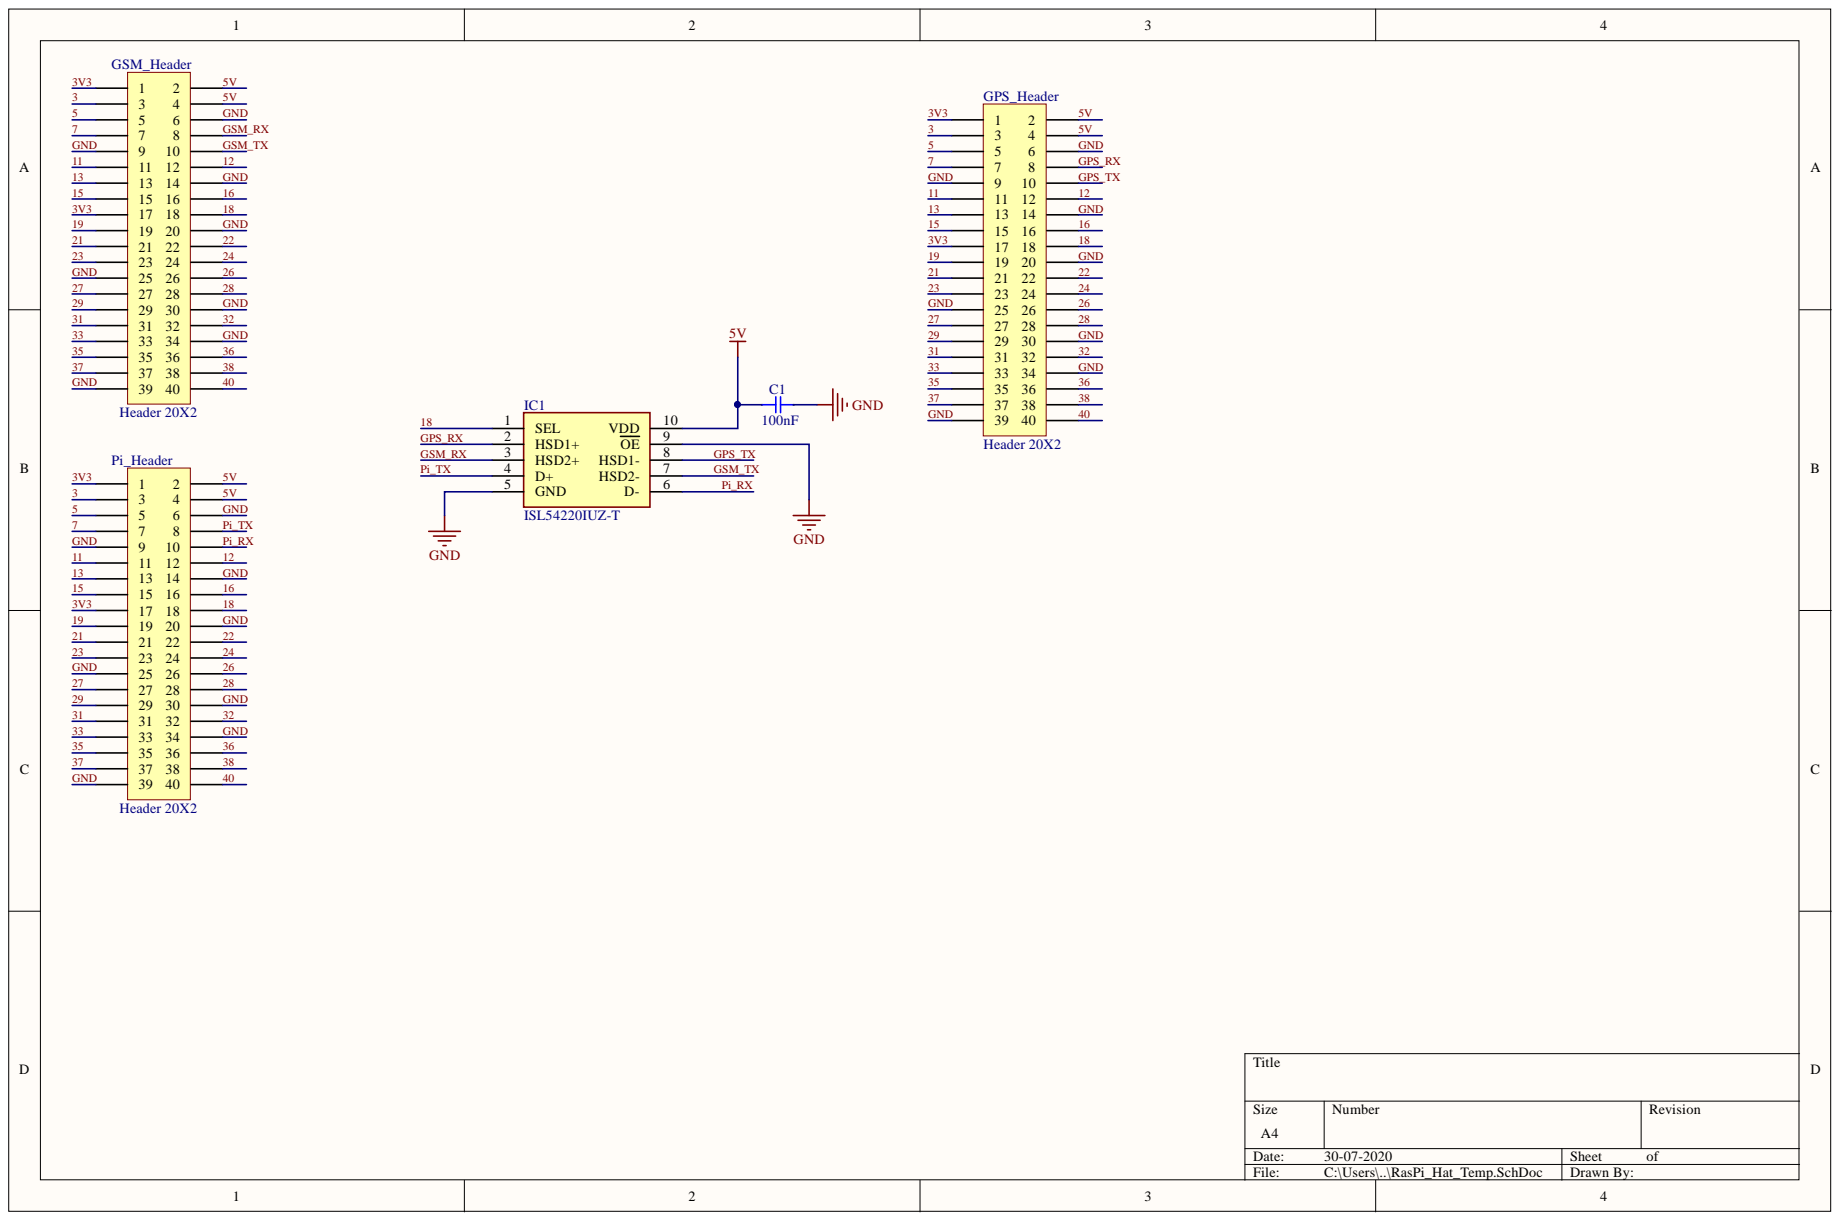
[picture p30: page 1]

Comment | Description | Designator | Footprint | LibRef | Quantity
100nF | CAP CER 1UF 10V X7SC1 | SMD-0402C | GCM155C71A105KE38 | 1
Header 20X2 | Header, 20-Pin, Dual roGPS_Header, GSM_HeadHD R2X20 | Header 20X2 | 3
ISL54220IUZ-T | Integrated Circuit | IC1 | SOP50P490X110-10N | ISL54220IUZ-T | 1

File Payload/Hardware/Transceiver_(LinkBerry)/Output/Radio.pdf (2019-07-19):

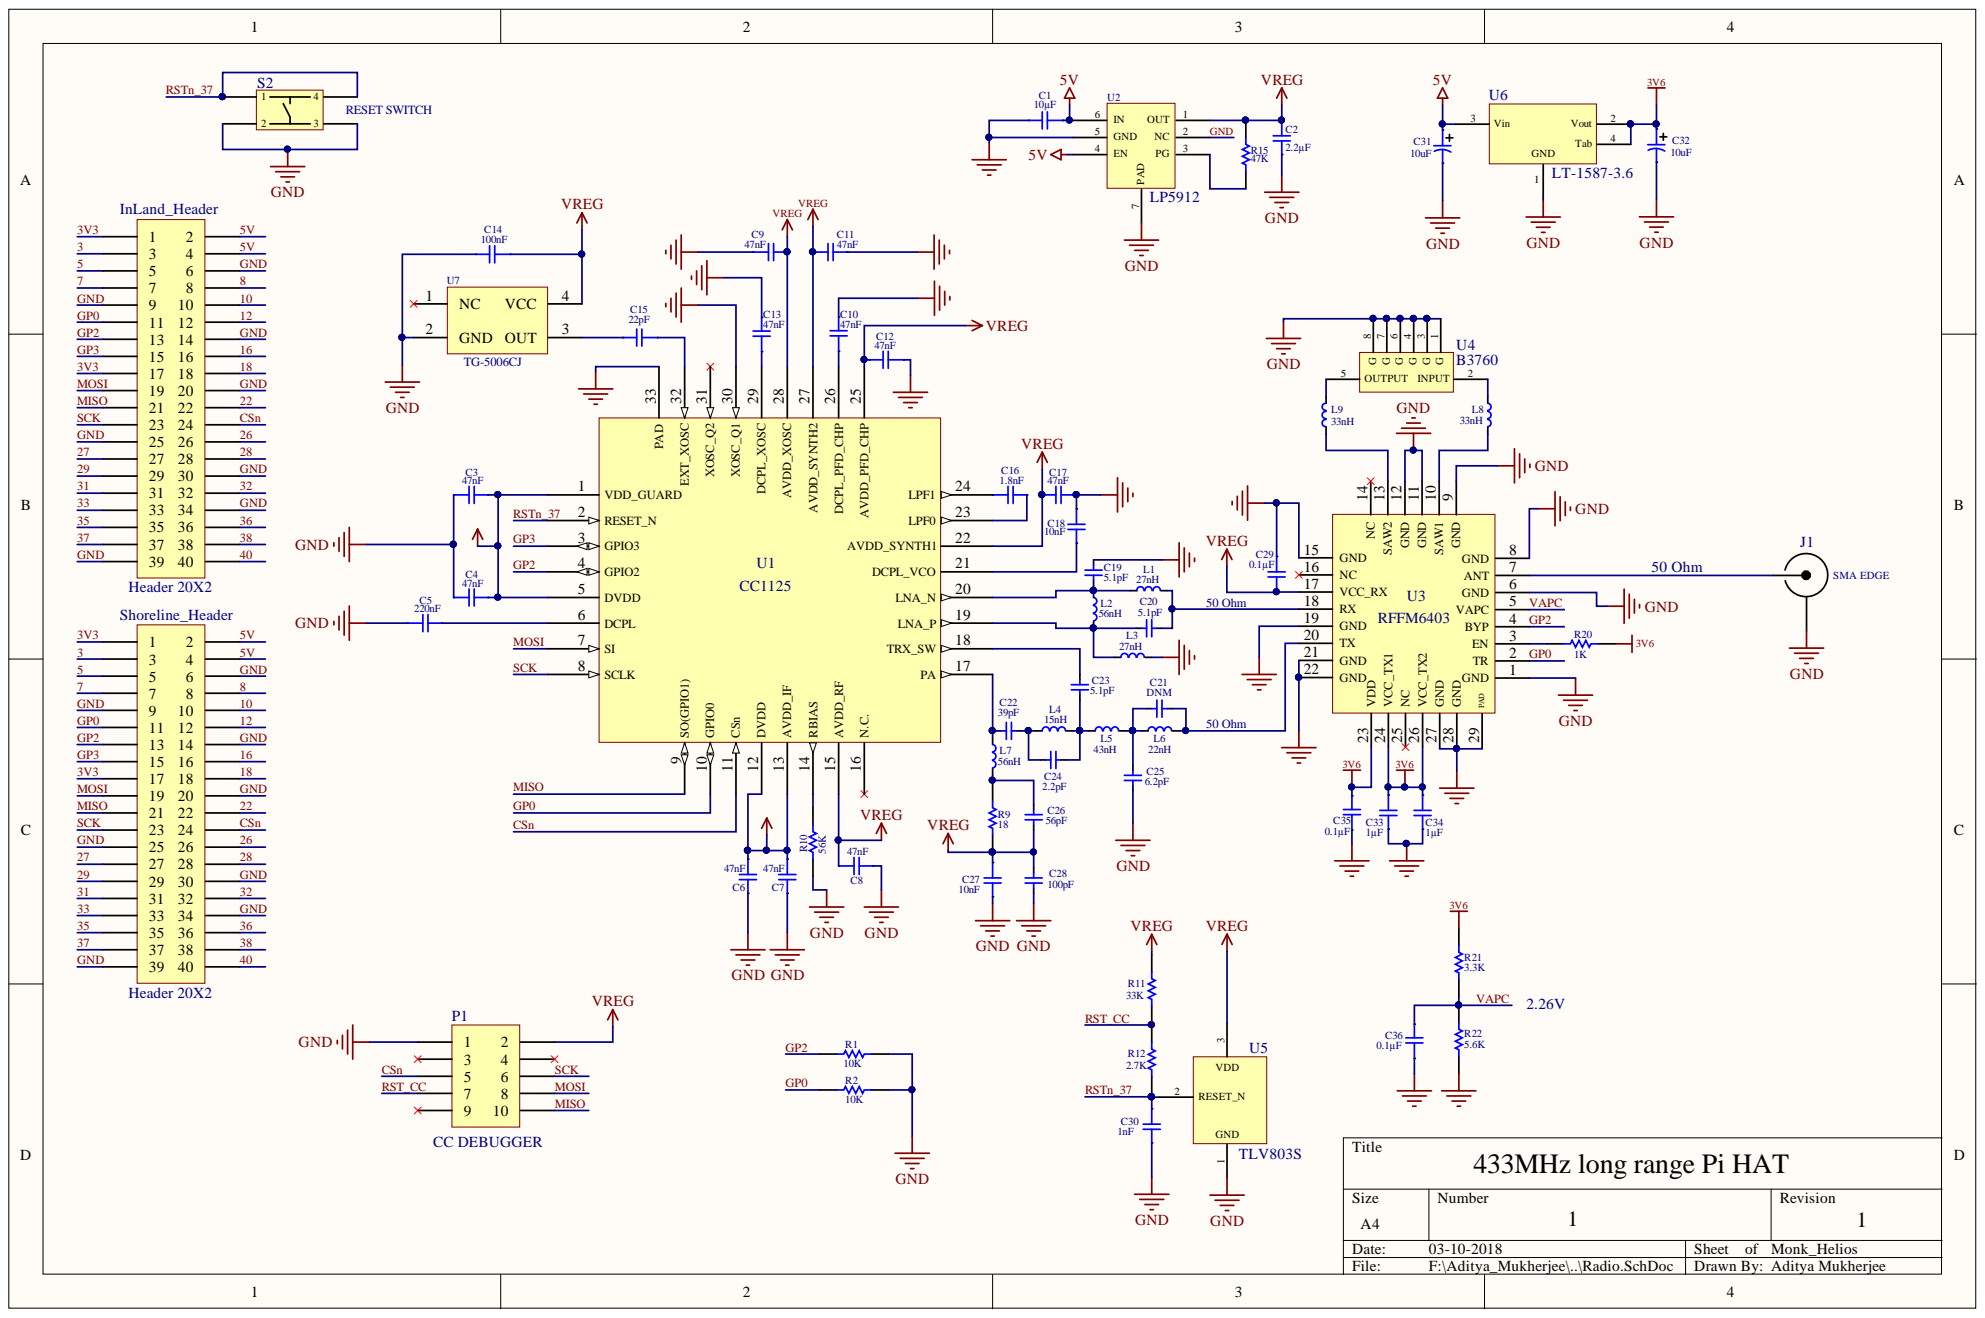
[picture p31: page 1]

DCPL 6 | | 50 Ohm | RX 18 | VAPC

GND 19 | GP2

433MHz long range Pi HAT

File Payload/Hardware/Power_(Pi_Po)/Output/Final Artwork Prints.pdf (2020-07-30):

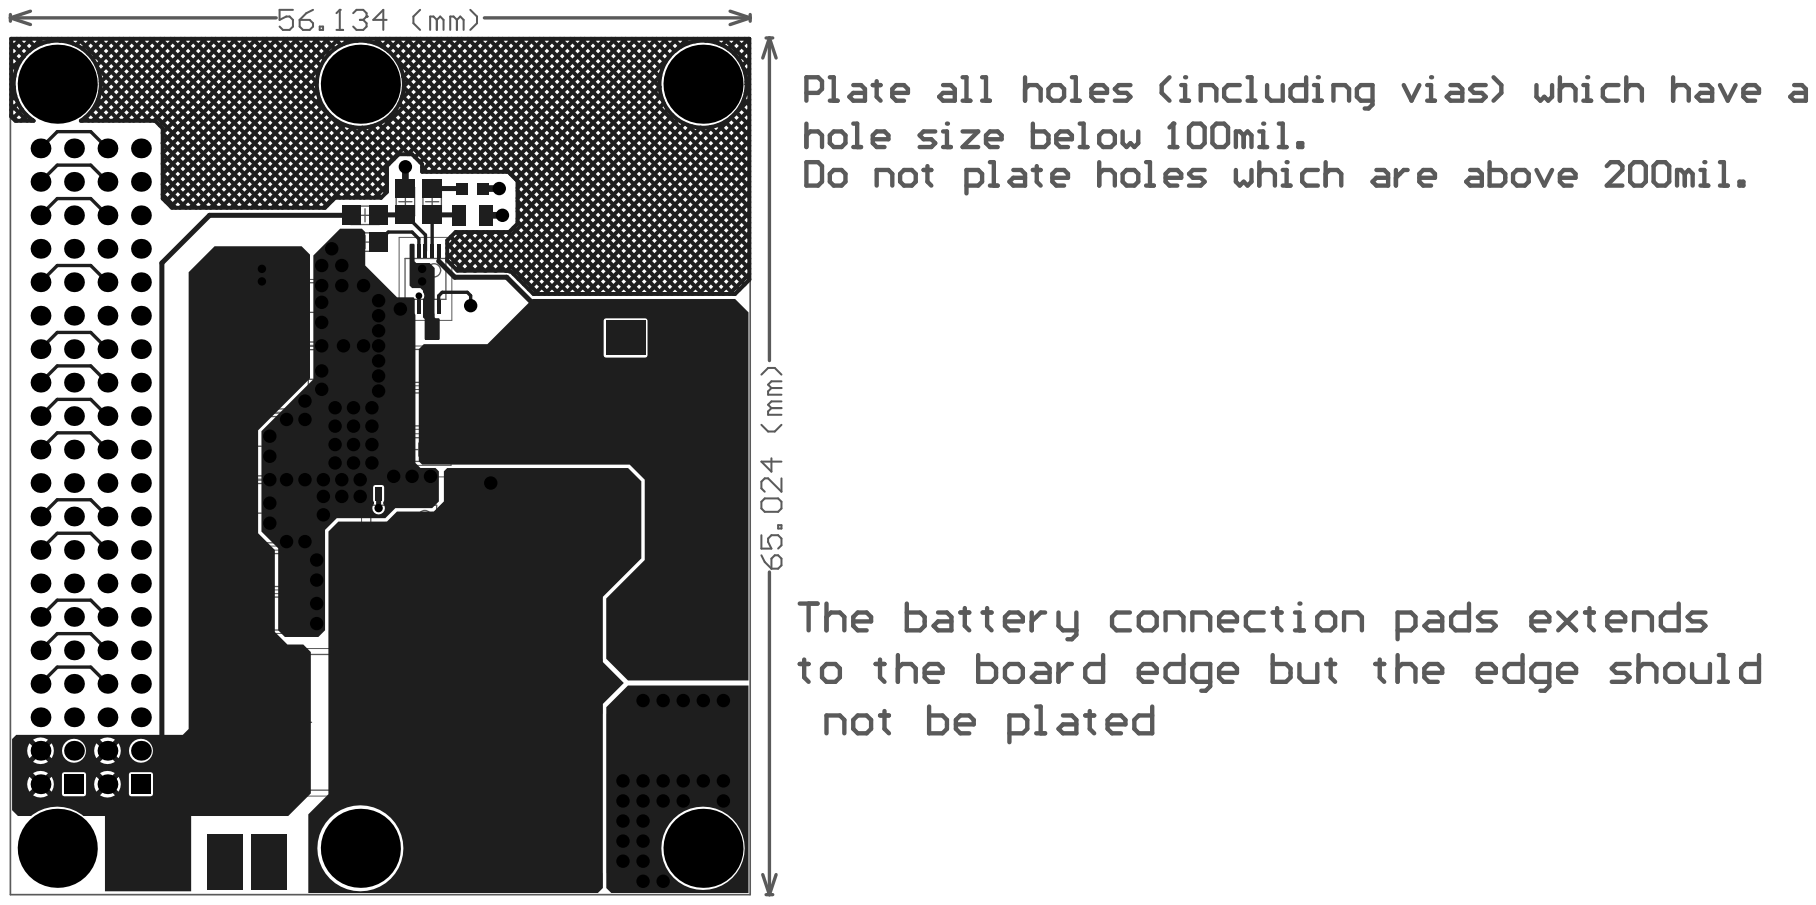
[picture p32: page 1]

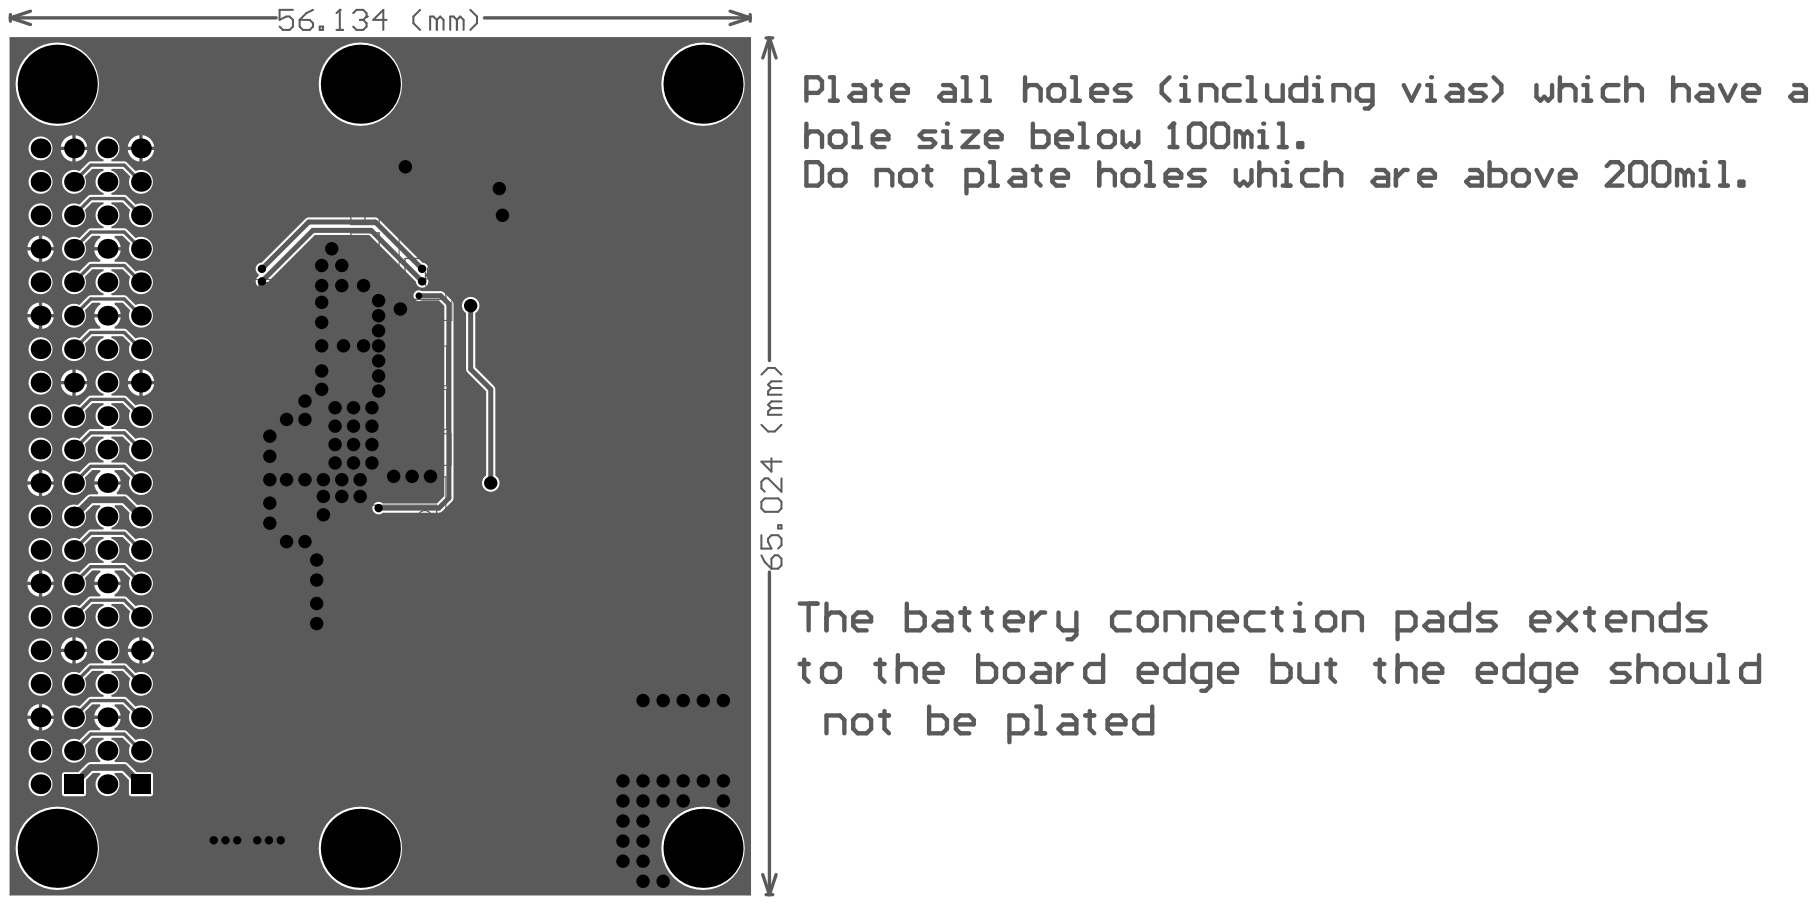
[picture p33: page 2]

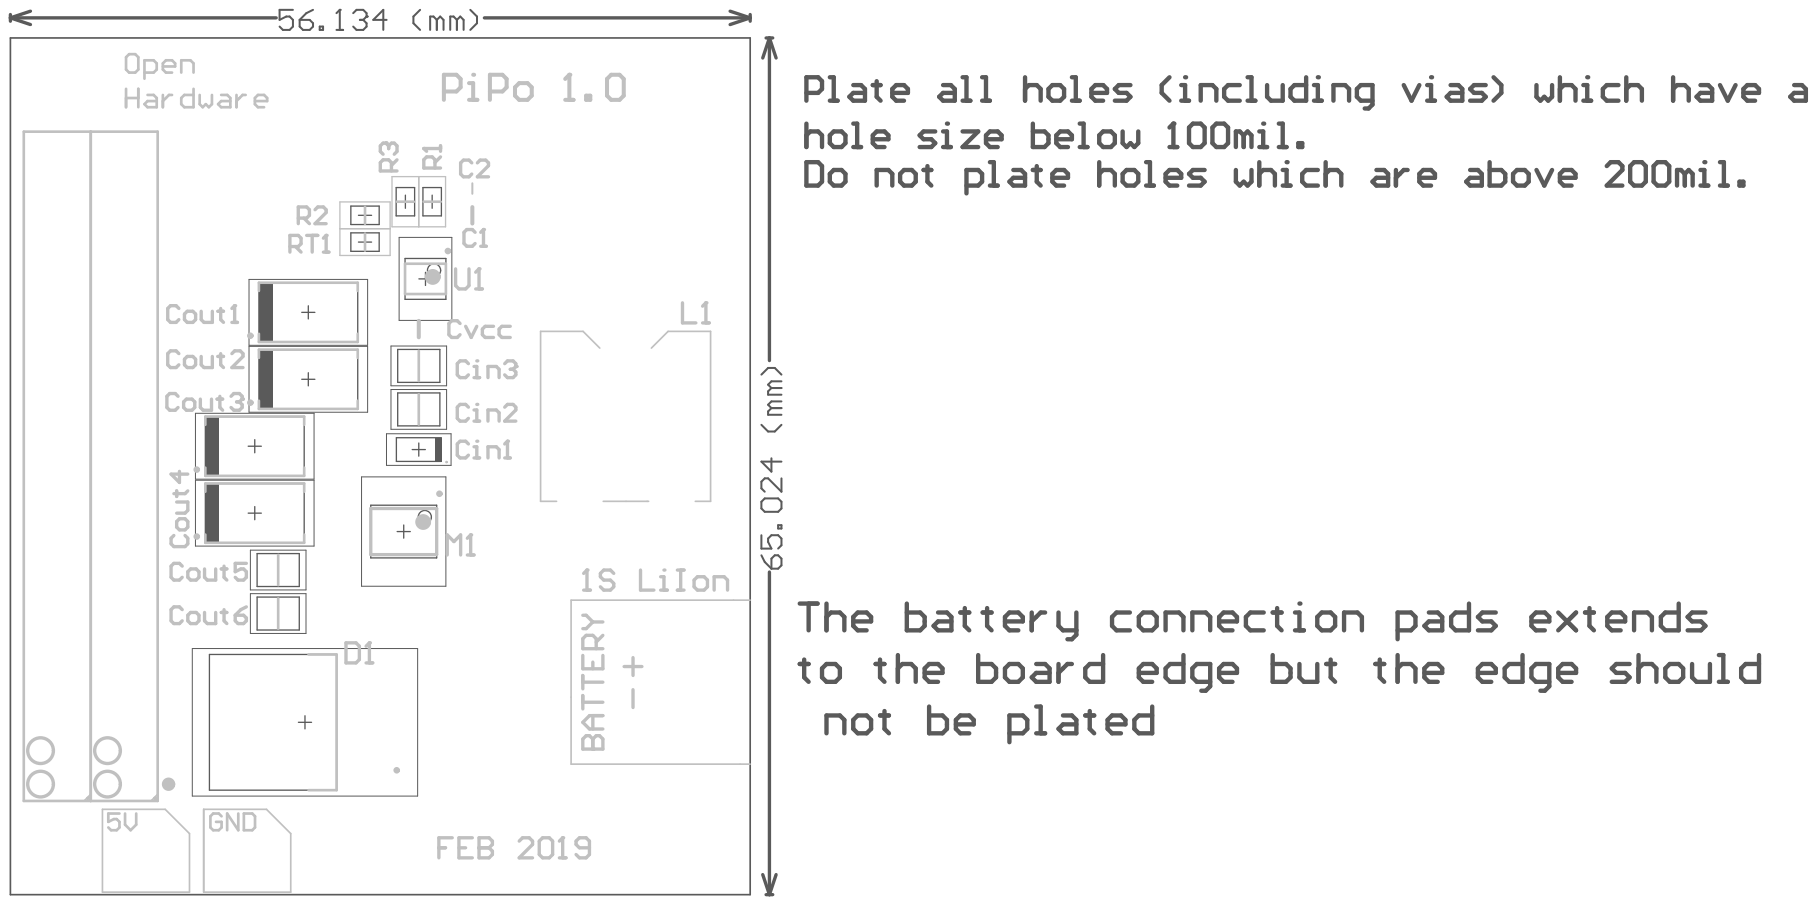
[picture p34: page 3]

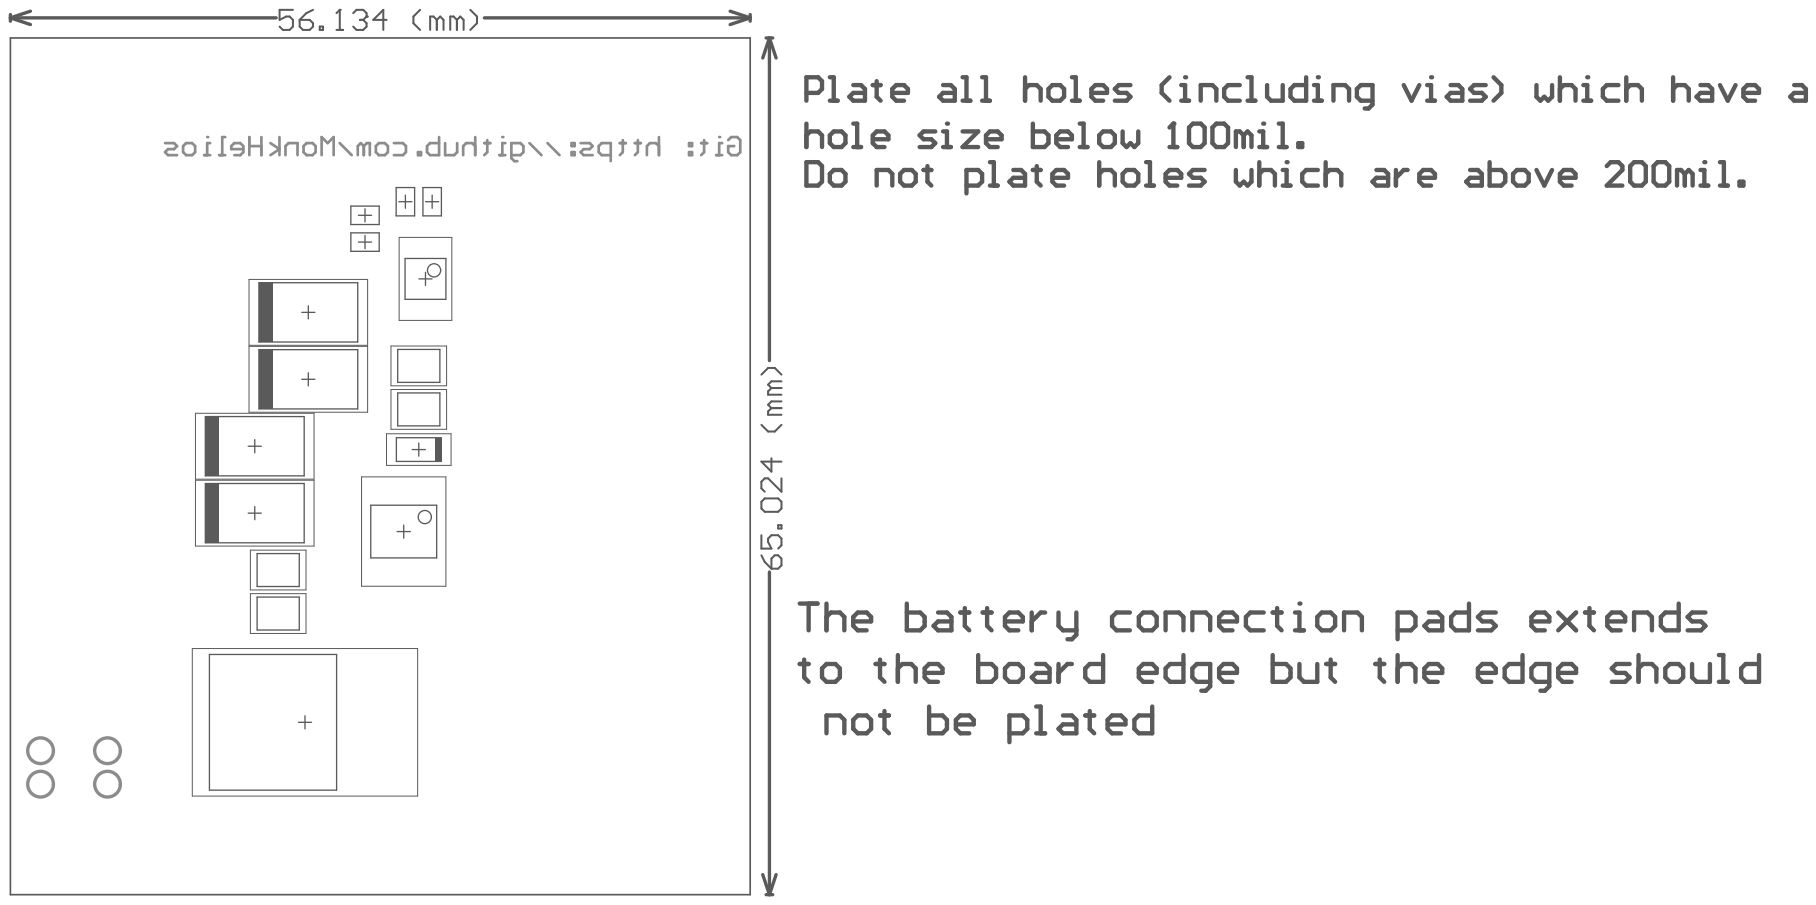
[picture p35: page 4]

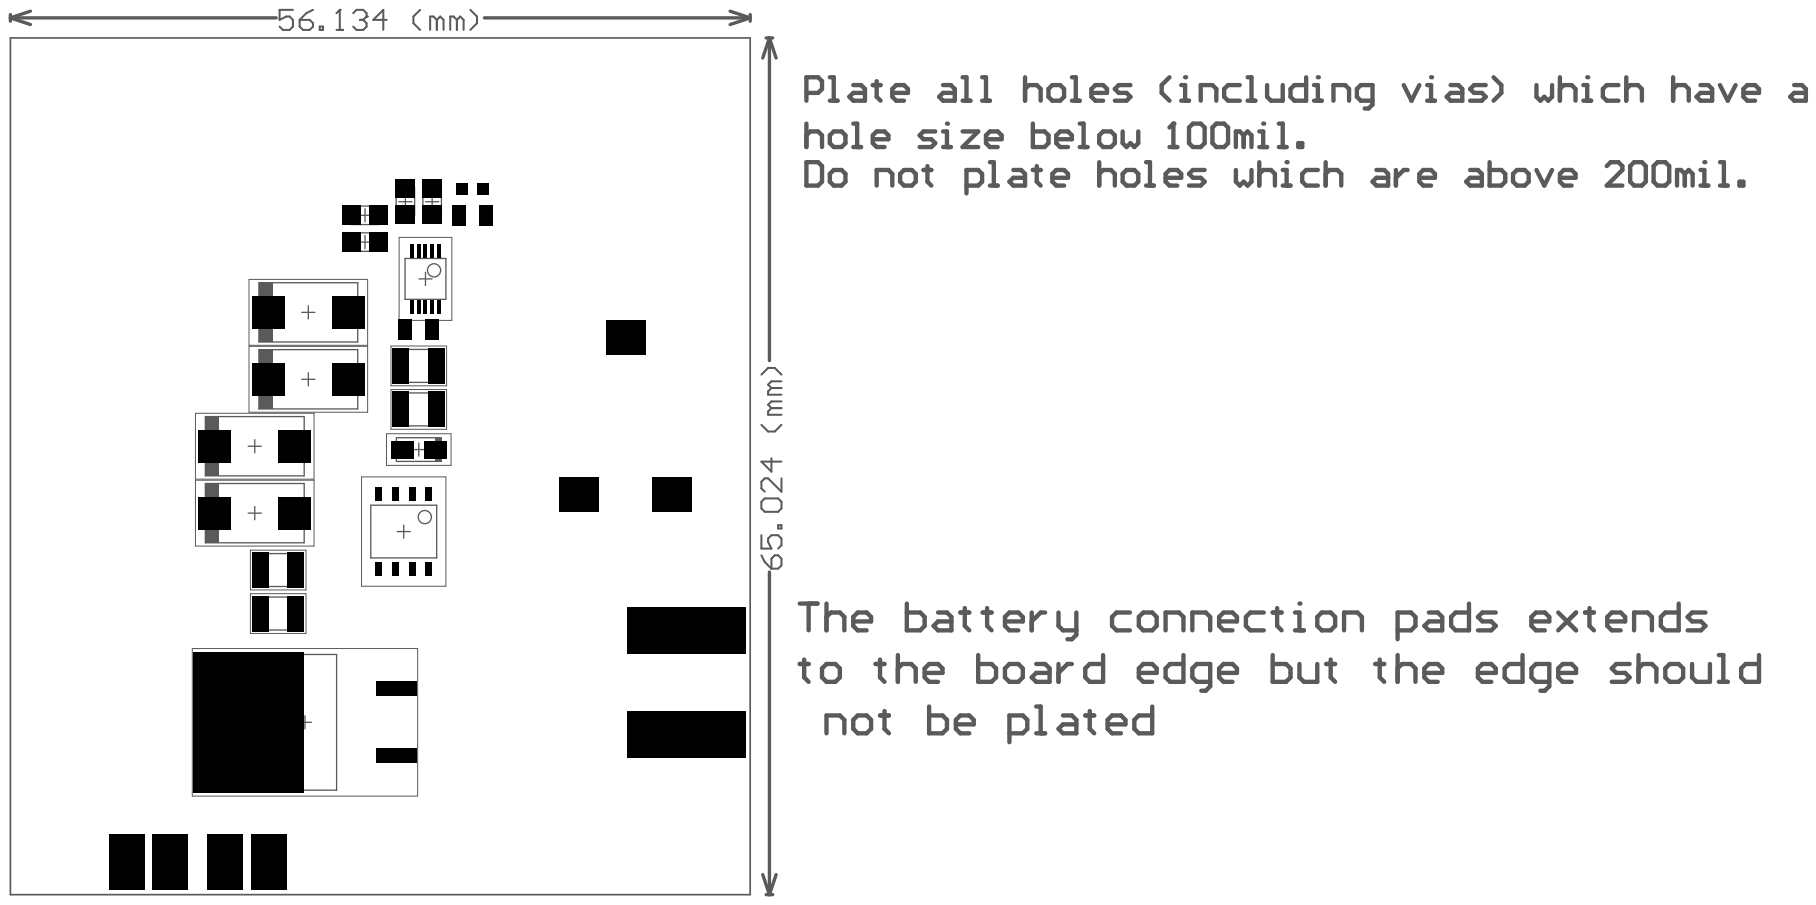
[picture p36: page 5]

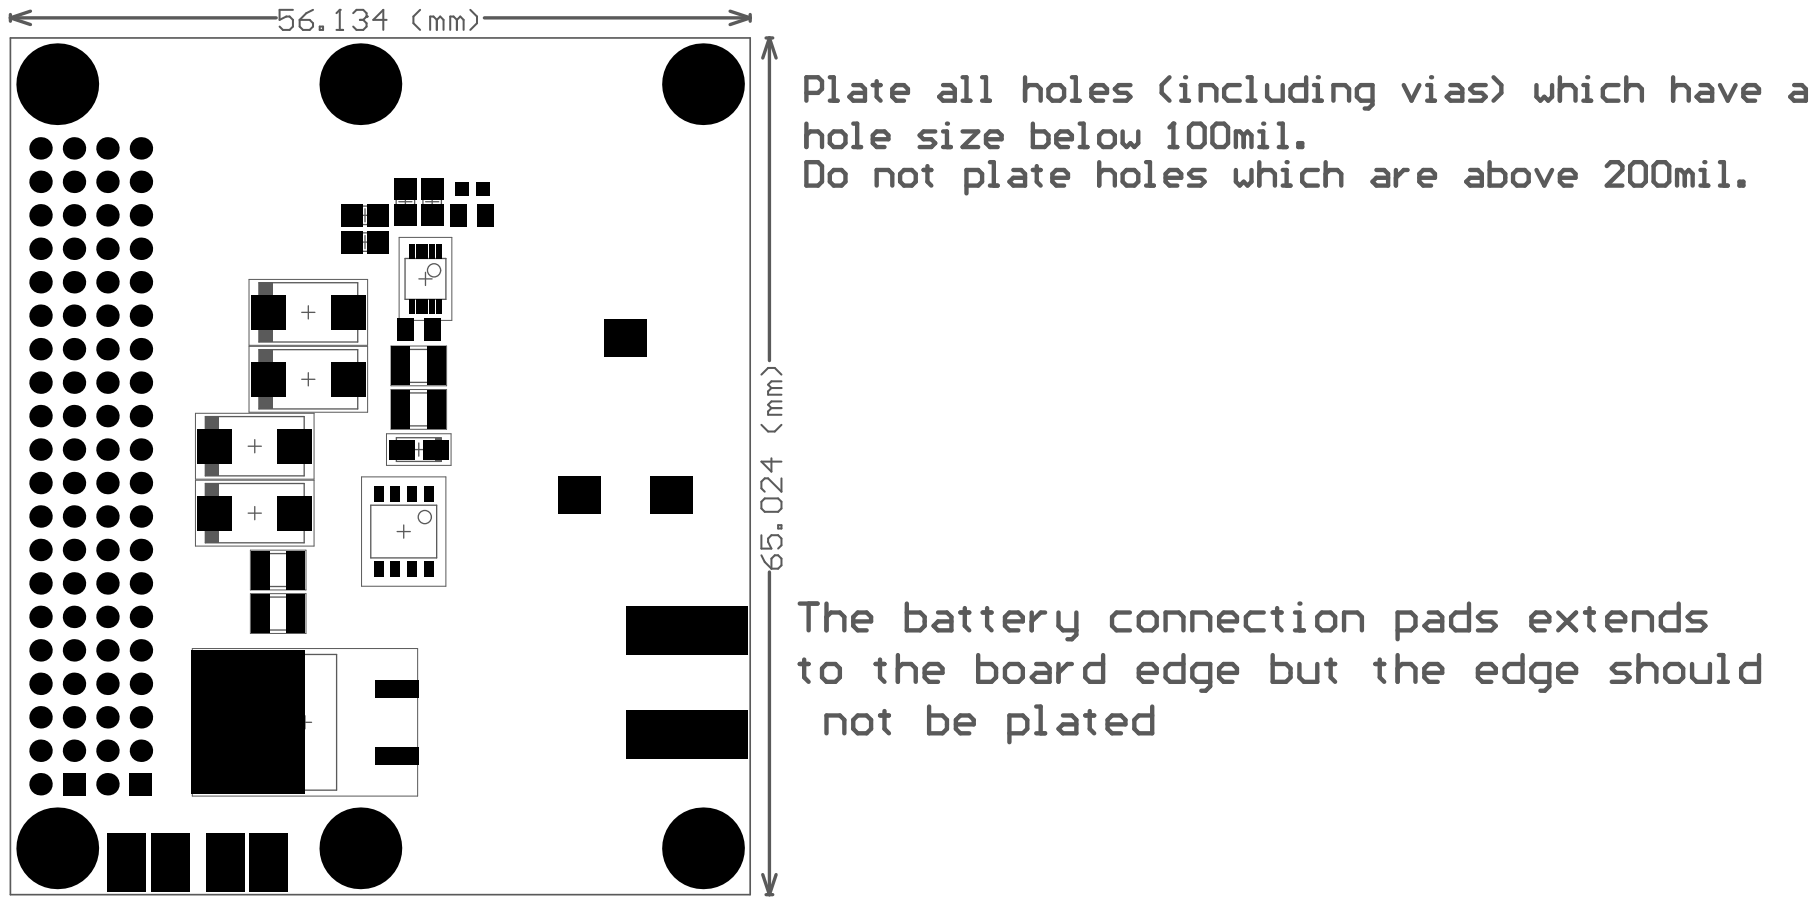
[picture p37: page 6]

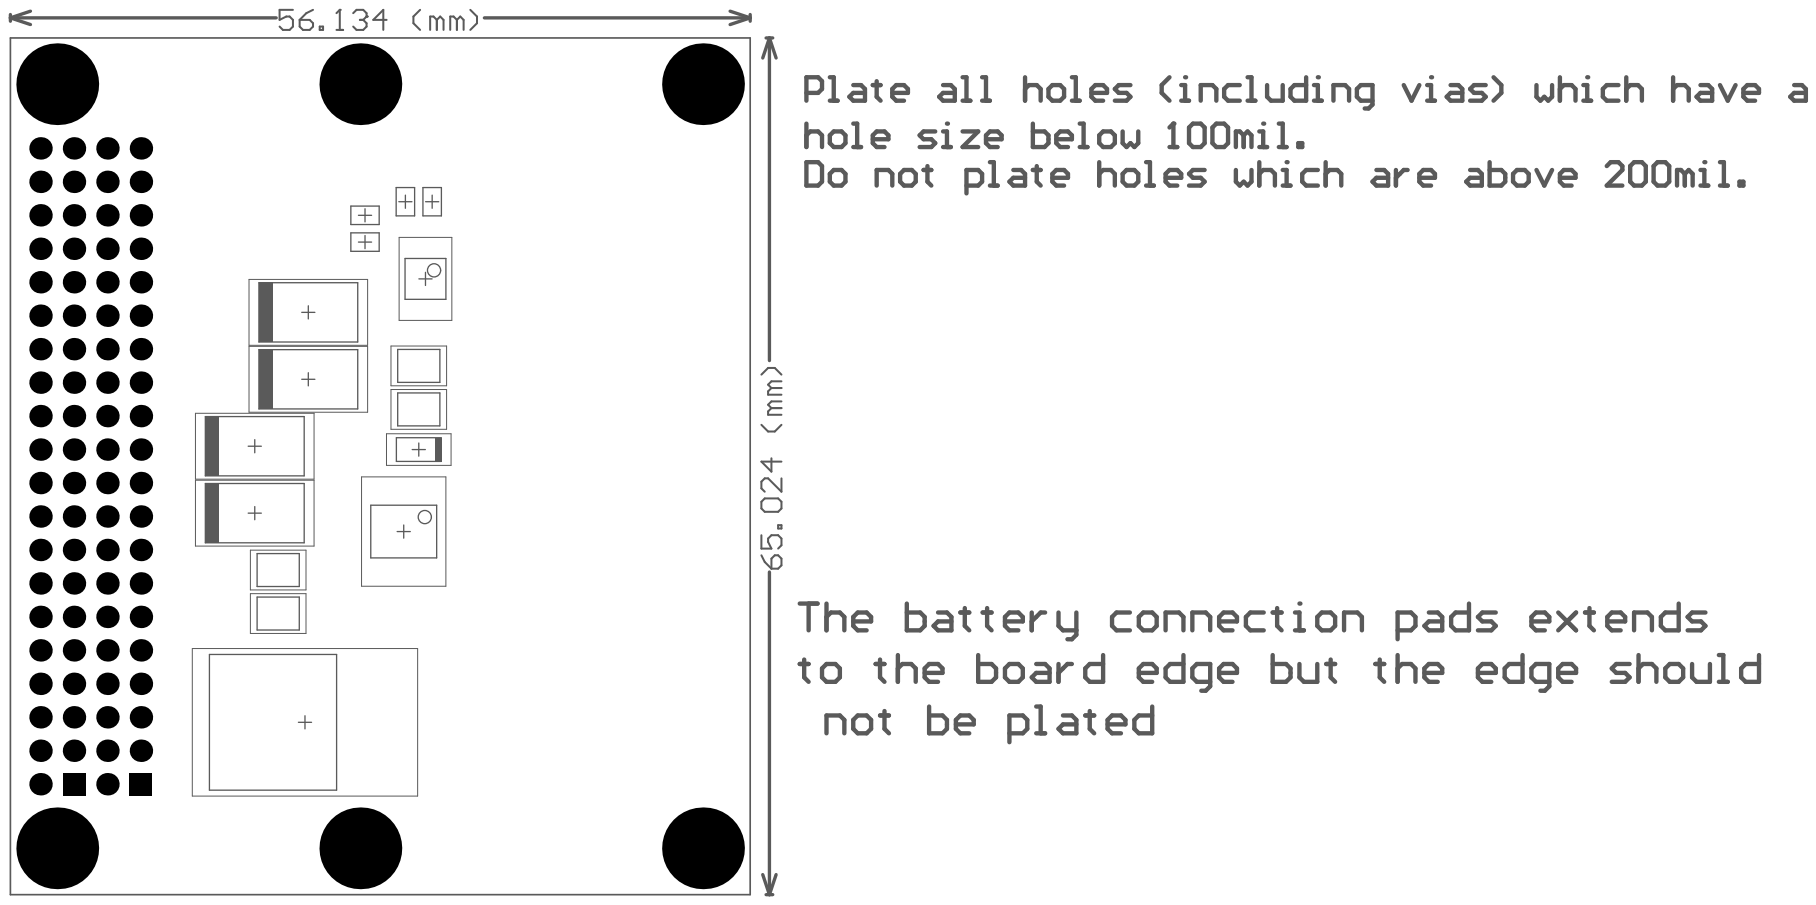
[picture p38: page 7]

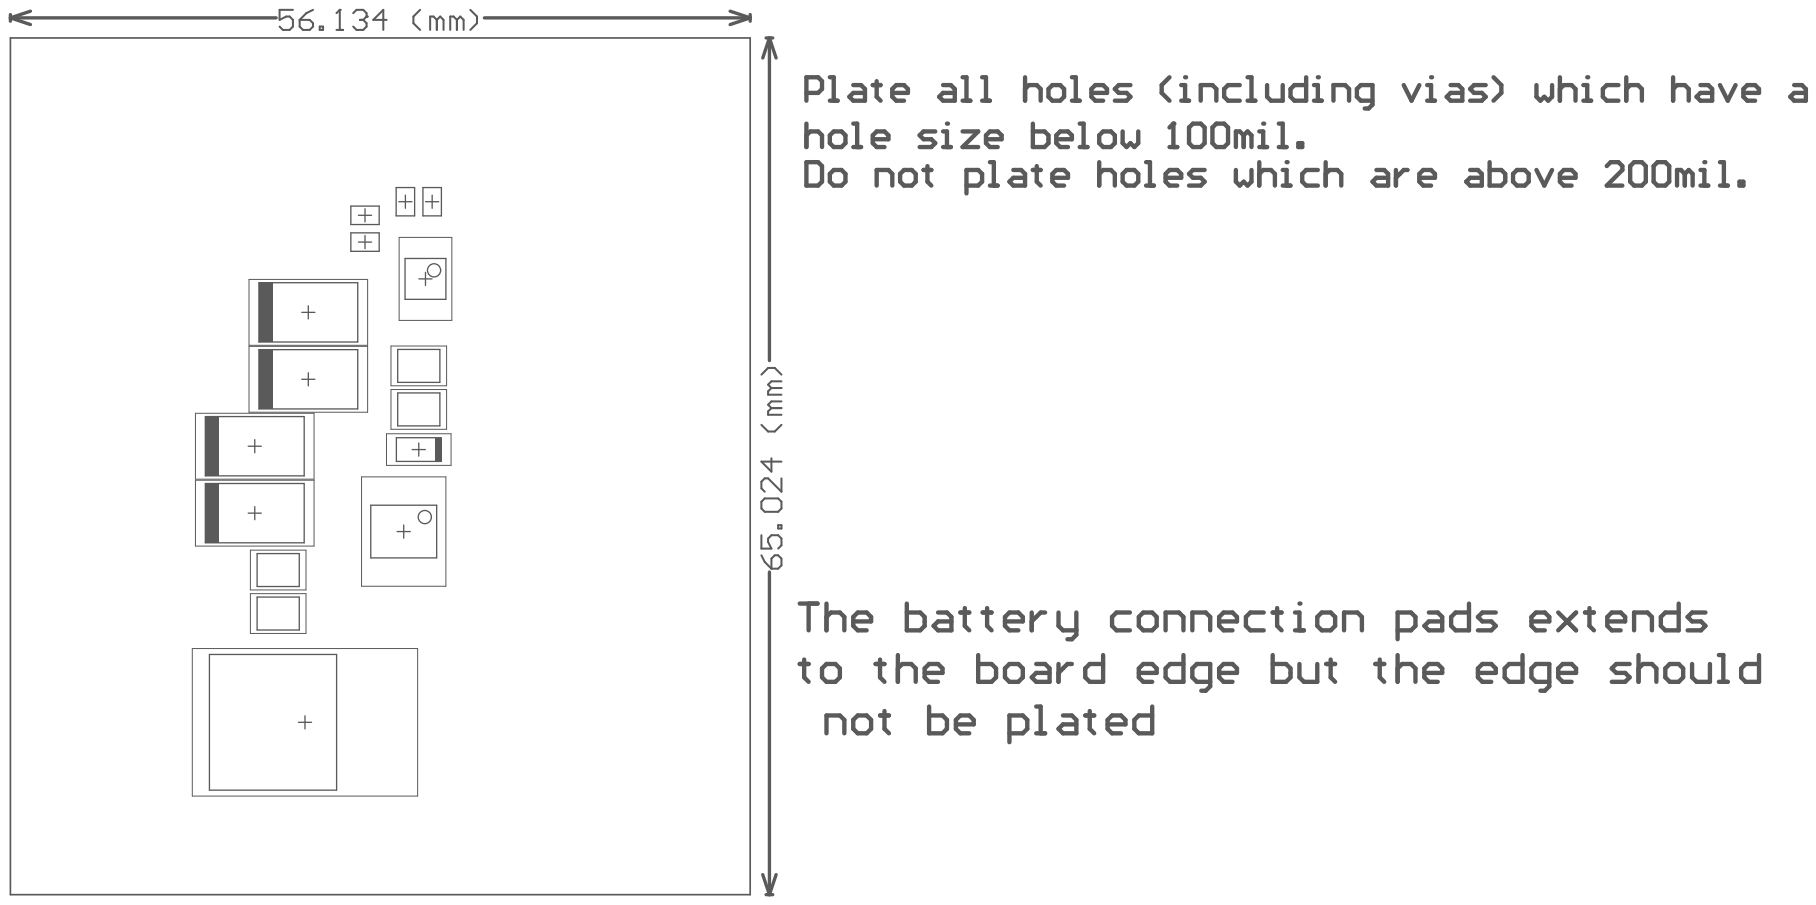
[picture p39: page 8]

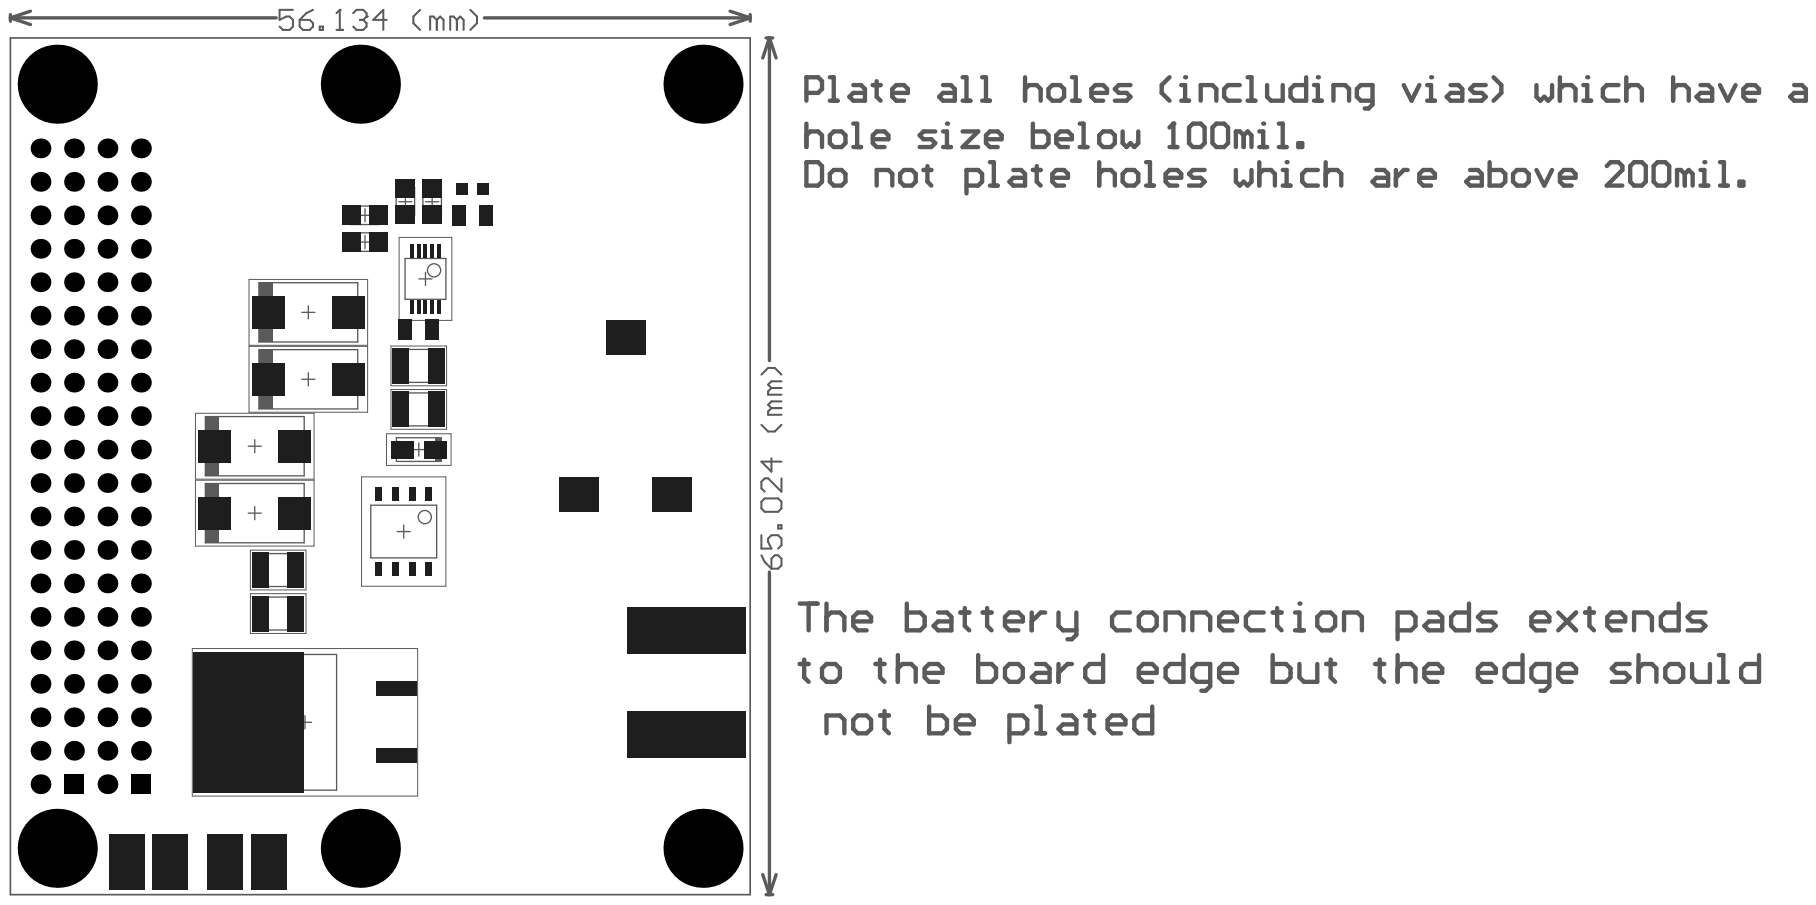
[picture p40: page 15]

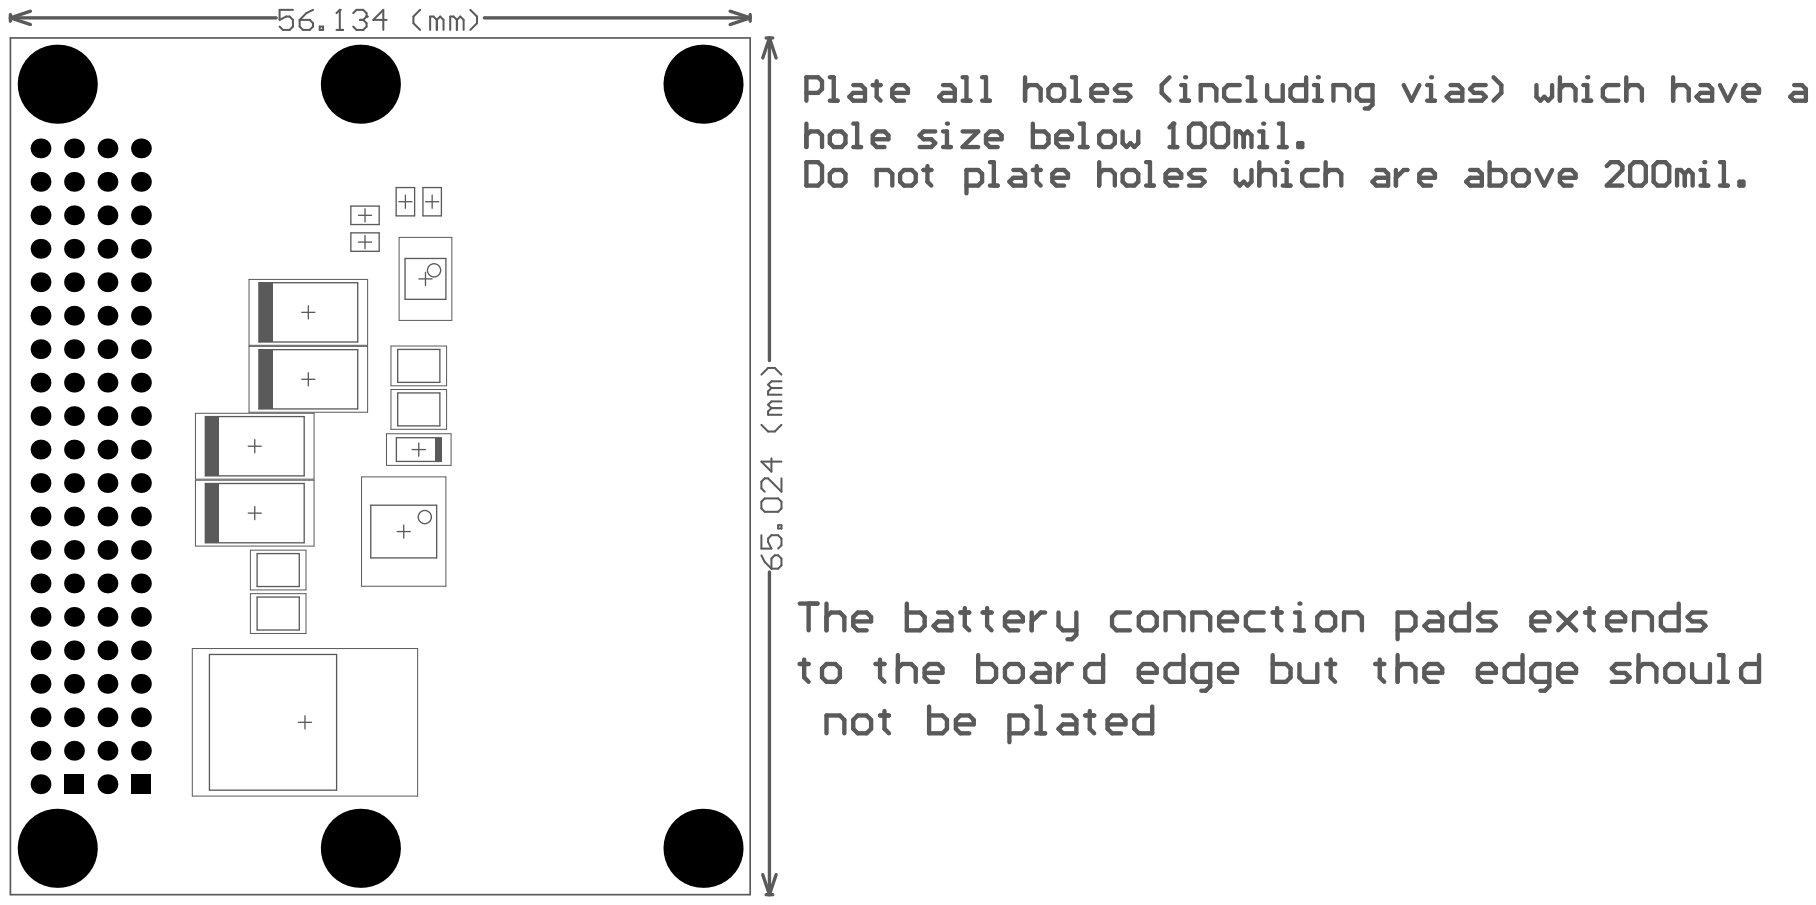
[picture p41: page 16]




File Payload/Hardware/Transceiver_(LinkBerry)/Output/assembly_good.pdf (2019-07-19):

A

B


Note:
1 Text element with square border.

2. Text element with no border

3 Text element with circle border

UNLESS OTHERWISE SPECIFIED:
DIMENSIONS ARE IN INCHES
TOLERANCES:
FRACTIONAL±
ANGULAR: MACH± BEND ±
TWO PLACE DECIMAL ±
THREE PLACE DECIMAL ±
INTERPRET GEOMETRIC
TOLERANCING PER:
MATERIAL

THE INFORMATION CONTAINED IN
THIS DRAWING IS THE SOLE
PROPERTY OF
. ANY REPRODUCTION IN PART OR
AS A WHOLE WITHOUT THE
WRITTEN PERMISSION OF IS











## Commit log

2020-07-26 Design files added and organised
    [BOM and PnP - CC1120 SKY65367-11 EM Ref Design Italy Rev1_0_2.xls, BOM.CSV, BOM.xlsx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]
2020-07-28 power board images addes
    [BOM.CSV, BOM.xlsx, PiPo.PrjPcb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]
2020-07-28 assembly of linkberry
2020-07-28 linkberry assembly pictures
2020-07-29 pipo schematic
